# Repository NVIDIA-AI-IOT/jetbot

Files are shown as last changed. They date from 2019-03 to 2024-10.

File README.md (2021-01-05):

# JetBot

<!--[<img src="https://img.shields.io/discord/553852754058280961.svg">](https://discord.gg/Ady6NtF) -->

> Looking for a quick way to get started with JetBot?  Many third party kits are [now available](https://jetbot.org/master/third_party_kits.html)!



JetBot is an open-source robot based on NVIDIA Jetson Nano that is

* **Affordable** - Less than $150 add-on to Jetson Nano
* **Educational** - Tutorials from basic motion to AI based collision avoidance
* **Fun!** - Interactively programmed from your web browser

Building and using JetBot gives the hands on experience needed to create entirely new AI projects.

To get started, read the [JetBot documentation](https://jetbot.org).

## Get involved

We really appreciate any feedback related to JetBot, and also just enjoy seeing what you're working on!  There is a growing community of Jetson Nano and JetBot users.  It's easy to get involved involved...

<!--* Join the [chat server](https://discord.gg/Ady6NtF)-->
* Ask a question and discuss JetBot related topics on the [JetBot GitHub Discussions](https://github.com/NVIDIA-AI-IOT/jetbot/discussions)
* Report a bug by [creating an issue](https://github.com/NVIDIA-AI-IOT/jetbot/issues)
* Share your project or ask a question on the [Jetson Developer Forums](https://devtalk.nvidia.com/default/board/139/jetson-embedded-systems/)

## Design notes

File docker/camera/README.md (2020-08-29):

# Camera Container

This container includes

* A launch script to publish camera images using ZMQ for access in other containers

#### Build

```bash
cd docker/camera
./build.sh
```

#### Run

```bash
cd docker/camera
./enable.sh
```

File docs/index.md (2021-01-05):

# JetBot

<!--[<img src="https://img.shields.io/discord/553852754058280961.svg">](https://discord.gg/Ady6NtF) -->

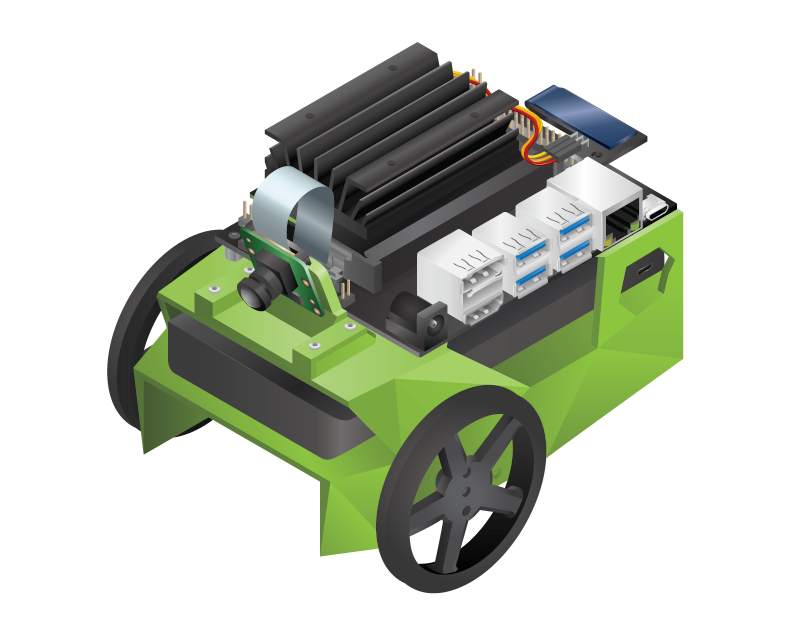
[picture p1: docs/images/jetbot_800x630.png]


<div style="text-align: left;">
    <a href="https://github.com/NVIDIA-AI-IOT/jetbot" class="md-button">Go to GitHub</a>
    <a href="getting_started.html" class="md-button md-button--primary">Get Started</a>
</div>

JetBot is an open-source robot based on NVIDIA Jetson Nano.  You'll like
it because...

## It's Affordable

<div style="display: inline-block">
    
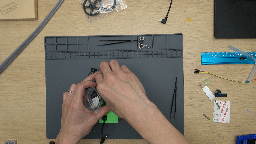
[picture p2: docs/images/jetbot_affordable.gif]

    
JetBot costs less than $250 in parts, <i>including</i> Jetson Nano. The DIY kit includes a bill of materials
which you must purchase and a 3D printed chassis that you can print, or order.  If you're looking to get
up and running as quick as possible, there are also many <a href="third_party_kits.html">third party kits</a> available
that come pre-bundled.

</div>

## It's Educational

<div style="display: inline-block">



JetBot includes a set of <a href="https://jupyter.org/">Jupyter notebooks</a> which cover basic robotics concepts like programatic motor control, to more advanced topics like training a custom AI for avoiding collisions.  What you'll learn isn't limited to JetBot.  You'll learn concepts related to neural network data collection and training that extend as far as your imagination.

</div>

## It's Easy to Setup

<div style="display: inline-block">

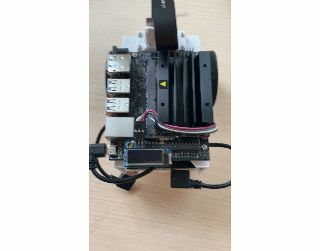
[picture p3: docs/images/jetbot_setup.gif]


JetBot is programmed from your web browser.  Just connect your JetBot to Wifi and launch the JetBot <a href="software_setup/docker.html">Docker container</a>.  This enables JetBot's web programming environment, which is available even after the JetBot reboots.  Once your JetBot boots, just type it's IP address into your web browser and start programming.  

</div>

## It's Fun!

<div style="display: inline-block">



We built JetBot to make exploring ideas related to robotics as fun as possible.  In effect, it's a portable, battery powered
AI computer with a camera that's super easy to program.  This makes it the perfect platform for trying new ideas
related to AI, image processing and robotics.  Our experiments have led us to new projects like <a href="https://github.com/NVIDIA-AI-IOT/jetracer">JetRacer</a>, and we're excited to see where your experiments take you.

</div>

## Get Started

To get started with JetBot, follow the [Getting Started](getting_started.md) instructions.  If you run into any issues along the way, please [let us know](https://github.com/NVIDIA-AI-IOT/jetbot/issues)!

<div style="text-align: right;">
    <a href="https://github.com/NVIDIA-AI-IOT/jetbot" class="md-button">Go to GitHub</a>
    <a href="getting_started.html" class="md-button md-button--primary">Get Started</a>
</div>

## Get involved

We really appreciate any feedback related to JetBot, and also just enjoy seeing what you're working on!  There is a growing community of Jetson Nano and JetBot users.  It's easy to get involved involved...

<!--* Join the [chat server](https://discord.gg/Ady6NtF)-->
* Ask a question and discuss JetBot related topics on the [JetBot GitHub Discussions](https://github.com/NVIDIA-AI-IOT/jetbot/discussions)
* Report a bug by [creating an issue](https://github.com/NVIDIA-AI-IOT/jetbot/issues)
* Share your project or ask a question on the [Jetson Developer Forums](https://devtalk.nvidia.com/default/board/139/jetson-embedded-systems/)

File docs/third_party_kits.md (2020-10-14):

# Third Party Kits

In addition to the open-source DIY version, several third party JetBot kits using Jetson Nano have emerged.  This page details the kits that we're aware of

???+ note 
    Please note, we do not officially maintain these kits in this GitHub project.  Please refer to the vendor's documentation. Please refer to the vendor URL for cost and availability.  Some kits may have additional vendors that we aren't aware of or haven't listed yet.  If you think these would be helpful for other developers to know, please [let us know](../../issues).

## Waveshare JetBot
    
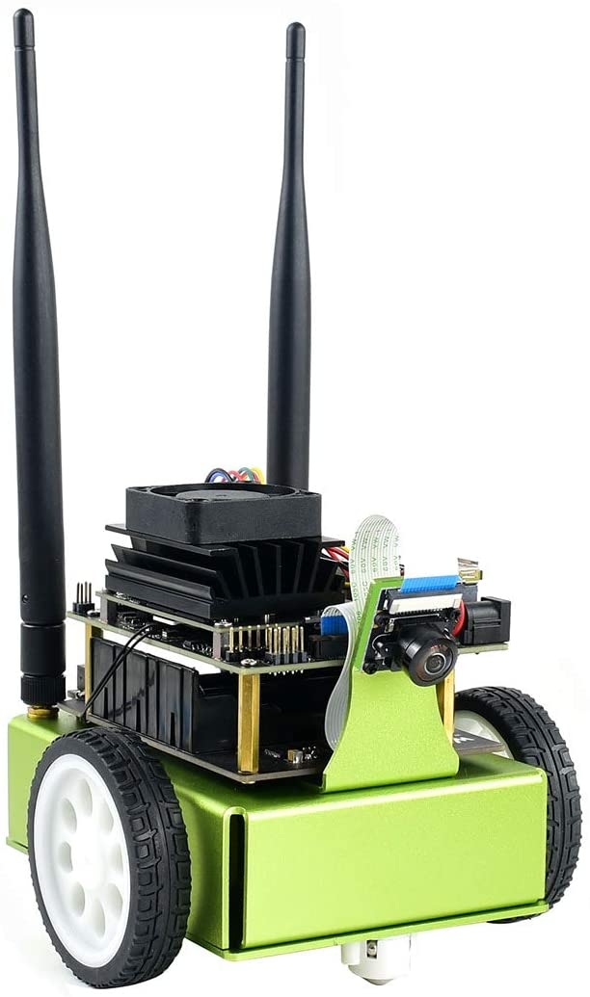
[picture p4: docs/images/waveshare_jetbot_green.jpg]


| Kit | URL |
|---|-----|
| WaveShare JetBot Kit |[Amazon.com](https://www.amazon.com/dp/B081LF98T8/), [Waveshare.com](https://www.waveshare.com/product/mini-pc/jetson/packages/jetbot-ai-kit-acce.htm), [Waveshare.net(中文)](https://www.waveshare.net/shop/JetBot-AI-Kit-Acce.htm) |
| WaveShare JetBot Kit (includes Jetson Nano Dev Kit) | [Amazon.com](https://www.amazon.com/dp/B081LCJXML/), [Waveshare.com](https://www.waveshare.com/product/mini-pc/jetson/packages/jetbot-ai-kit.htm), [Waveshare.net(中文)](https://www.waveshare.net/shop/JetBot-AI-Kit.htm) |

### Links

- [JetBot AI Kit Assemble Manual](https://www.waveshare.com/wiki/JetBot_AI_Kit_Assemble_Manual)
- [JetBot AI Kit](https://www.waveshare.com/wiki/JetBot_AI_Kit)
- [JetBot AI Kit (中文)](https://www.waveshare.net/wiki/JetBot_AI_Kit)

## SparkFun JetBot



| Kit | URL |
|---|-----|
| SparkFun JetBot AI Kit v2.1 | [SparkFun](https://www.sparkfun.com/products/15769) |
| SparkFun JetBot AI Kit v2.1 (includes Jetson Nano Dev Kit) | [SparkFun](https://www.sparkfun.com/products/16417) |

### Links

- [Assembly Guide for SparkFun JetBot AI Kit V2.0](https://learn.sparkfun.com/tutorials/assembly-guide-for-sparkfun-jetbot-ai-kit-v20)

## Seeedstudio JetBot
    


| Kit | URL |
|---|-----|
| Seeedstudio JetBot Smart Car Kit | [Seeedstudio](https://www.seeedstudio.com/Seeedstudio-JetBot-Smart-Car-Kit-p-4055.html) |
| Seeedstudio JetBot Smart Car Kit (includes Jetson Nano Dev Kit) | [Seeedstudio](https://www.seeedstudio.com/Seeedstudio-JetBot-Smart-Car-Powered-by-NVIDIA-Jetson-Nano-p-4054.htm) |

### Links

- [Seeedstudio JetBot Wiring Guide](https://github.com/SeeedDocument/Seeedstudio-Jetbot-Smart-Car/raw/master/res/Seeed%20JetBot%20wiring%20Guide.pdf)
- [Seeedstudio JetBot Setup Guide](https://github.com/SeeedDocument/Seeedstudio-Jetbot-Smart-Car/raw/master/res/Jetbot-snail.docx)

## Silicon Highway JetBot



| Kit | URL |
|---|-----|
| Silicon Highway JetBot Kit | [Silicon Highway (UK)](https://www.siliconhighwaydirect.co.uk/product-p/jetbot-kit.htm) |

## FaBo JetBot
    


| Kit | URL |
|---|-----|
| FaBo JetBot Kit (with Jetson Nano Dev Kit) | [FaBo store (Japan)](https://www.fabo.store/collections/jetbot/products/jetbot-kit) |

### Links

- [JetBot Kit チュートリアル](https://faboplatform.github.io/JetbotDocs/)

## GPUS JetBot
    


| Kit | URL |
|---|-----|
| GPUS JetBot Kit (with Jetson Nano Dev Kit) | [Taobao](https://item.taobao.com/item.htm?id=602196310625) |

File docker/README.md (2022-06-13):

# JetBot Docker

This directory contains scripts to build the JetBot docker containers.  

## Quick Start

### Step 1 - Configure System

First, call the ``scripts/configure_jetson.sh`` script to configure the power mode and other parameters.

```bash
cd jetbot
./scripts/configure_jetson.sh
```

Next, source the ``docker/configure.sh`` script to configure various environment variables related to JetBot docker.

```bash
cd docker
source configure.sh
```

Depending on your Jetson L4T version, you may get a similar warning :

```bash
JETBOT_BASE_IMAGE not found for 32.6.1.  Please manually set the JETBOT_BASE_IMAGE environment variable. (ie: export JETBOT_BASE_IMAGE=...)
```

In the case of ``32.6.1``, the following container will work :

```bash
export JETBOT_BASE_IMAGE=nvcr.io/nvidia/l4t-pytorch:r32.6.1-pth1.9-py3
```

Refer to ``https://ngc.nvidia.com/catalog/containers/nvidia:l4t-pytorch`` for more details.

Finally, if you haven't already, set the default docker runtime to NVIDIA.  This is needed to use
CUDA related components with the containers.

```bash
./set_nvidia_runtime.sh
```

If needed, you can also set memory limits on the Jupyter container.

```bash
export JETBOT_JUPYTER_MEMORY=500m
export JETBOT_JUPYTER_MEMORY_SWAP=3G
```

### Step 2 - Building Containers

If you want to build the containers from scratch, simply call :

```bash
./build.sh
```

### Step 3 - Enable All Containers

Call the following to enable the JetBot docker containers 

```bash
sudo systemctl enable docker   # enable docker daemon at boot
./enable.sh $HOME   # we'll use home directory as working directory, set this as you please.
```

Now you can go to ``https://<jetbot_ip>:8888`` from a web browser and start programming JetBot!
You can do this from any machine on your local network.  The password to log in is ``jetbot``.



> Note: The directory you specify to ``./enable.sh`` will be mounted as a volume in the jupyter container 
at the location ``/workspace``.  This means the work you in the ``/workspace`` folder inside container
is saved.  This is set to the root directory of Jupyter Lab.  Please note, if you work outside of that directory it will be lost when the container shuts down.

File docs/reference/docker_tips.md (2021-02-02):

# Docker Tips

This page provides various information related to using docker with JetBot.

## Establishing access to the Docker host terminal

The Jupyter Lab is running in the Docker container, thus the **Terminal** you open on Jupyter Lab only have access to the container environment.<br>
This means you cannot use commands like `nvpmodel`, `tegrastats`, `journalctl`, `systemctl` and others.

To get around this limitation, you can actually SSH in to the Docker host machine by;

```
ssh jetbot@0.0.0.0
```

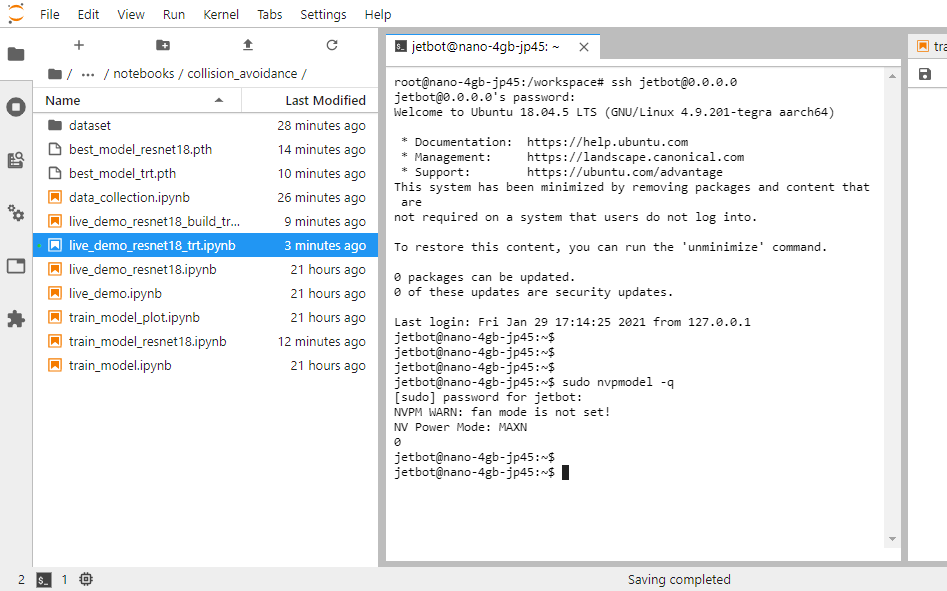
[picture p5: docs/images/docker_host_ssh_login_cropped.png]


## Using Nvidia GPU Cloud (NGC)

The standard JetBot containers are hosted on docker hub, but for development or testing purposes, you may wish to use Nvidia GPU Cloud. To access containers on NGC, you need to sign into the NGC registry. To do this:

1. Log into ngc.nvidia.com

2. Generated your API Key

    1. Navigate to Setup > API Key
    2. Click on "Generate API Key" at the right upper corner of the page
    3. Copy the API key for future use

3. On your Jetson, sign into the NGC registry using the generated key

    ```bash
    $ sudo docker login nvcr.io
    
    Username: $oauthtoken
    Password: <Your Generated Key>
    ```

For the username, enter `$oauthtoken` exactly as shown. It is a special authentication token for all users.

## Using custom Jupyter Lab workspace directory

The argument you provide to the enable.sh script is mounted as a volume inside the docker container. Inside the docker container, this volume is located at /workspace. Any changes that you make inside this directory will be saved outside of the docker container. To use a different directory as the workspace for the Jupyter contianer, just provide the path as an argument when calling enable.sh. For example, to set the workspace to your home directory, you would do

```bash
cd jetbot/docker
./enable.sh $HOME
```

## Disabling containers

Once you execute the `enable.sh` script, the containers are set to restart automatically.
This means you can shut down your Jetson, and when you reboot the containers will run and you don't need to repeat this process. 

To prevent the containers from starting automatically, just call the disable.sh script.

```bash
cd ~/jetbot/docker
./disable.sh
```

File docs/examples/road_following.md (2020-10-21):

# Road Following

In this example we'll collect an *image regression* dataset that will enable JetBot to follow a road!  We'll teach JetBot to detect a target ``x, y`` image coordinate that the JetBot will chase.  As JetBot gets closer to the point, it moves further along the track.

#### Step 1 - Collect data on JetBot

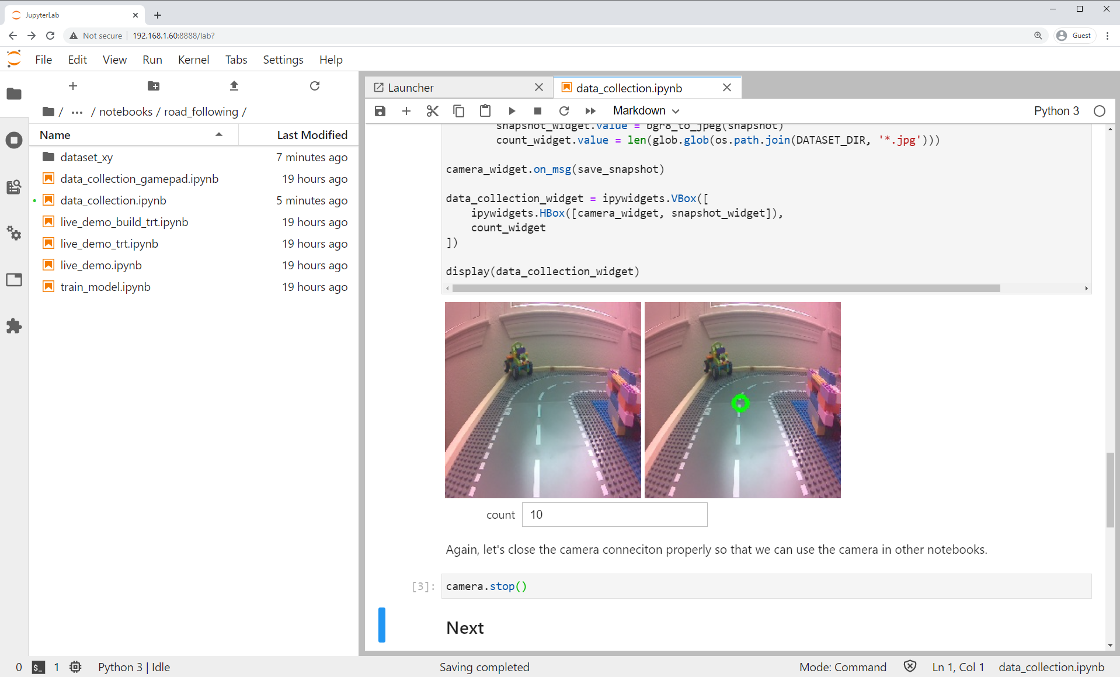
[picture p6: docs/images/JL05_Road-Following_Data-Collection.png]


1. Connect to your robot by navigating to ``http://<jetbot_ip_address>:8888``
2. Sign in with the default password ``jetbot``
2. Shutdown all other running notebooks by selecting ``Kernel`` -> ``Shutdown All Kernels...``
3. Navigate to ``~/Notebooks/road_following/``
4. Open and follow the ``data_collection.ipynb`` notebook

#### Step 2 - Train neural network

##### Option 1 - Train on Jetson Nano
1. Connect to your robot by navigating to ``http://<jetbot_ip_address>:8888``
2. Sign in with the default password ``jetbot``
3. In the Jupyter Lab tab, navigate to ``~/Notebooks/road_following``
4. Open and follow the [``train_model.ipynb``](https://github.com/NVIDIA-AI-IOT/jetbot/blob/master/notebooks/road_following/train_model.ipynb) notebook

##### Option 2 - Train on other GPU machine
1. Connect to a GPU machine with PyTorch installed and a Jupyter Lab server running

2. Upload the road following avoidance [training notebook](https://github.com/NVIDIA-AI-IOT/jetbot/blob/master/notebooks/road_following/train_model.ipynb) to this machine
3. Open and follow the ``train_model.ipynb`` notebook

#### Step 3 - Optimize the model on Jetson Nano

1. Connect to your robot by navigating to ``https://<jetbot_ip_address>:8888``
2. Sign in with the default password ``jetbot``
3. Shutdown all other running notebooks by selecting ``Kernel`` -> ``Shutdown All Kernels...``
4. Navigate to ``~/Notebooks/road_following``
5. Open and follow the ``live_demo_build_trt.ipynb`` notebook to optimize the model with TensorRT

#### Step 4 - Run live demo on JetBot

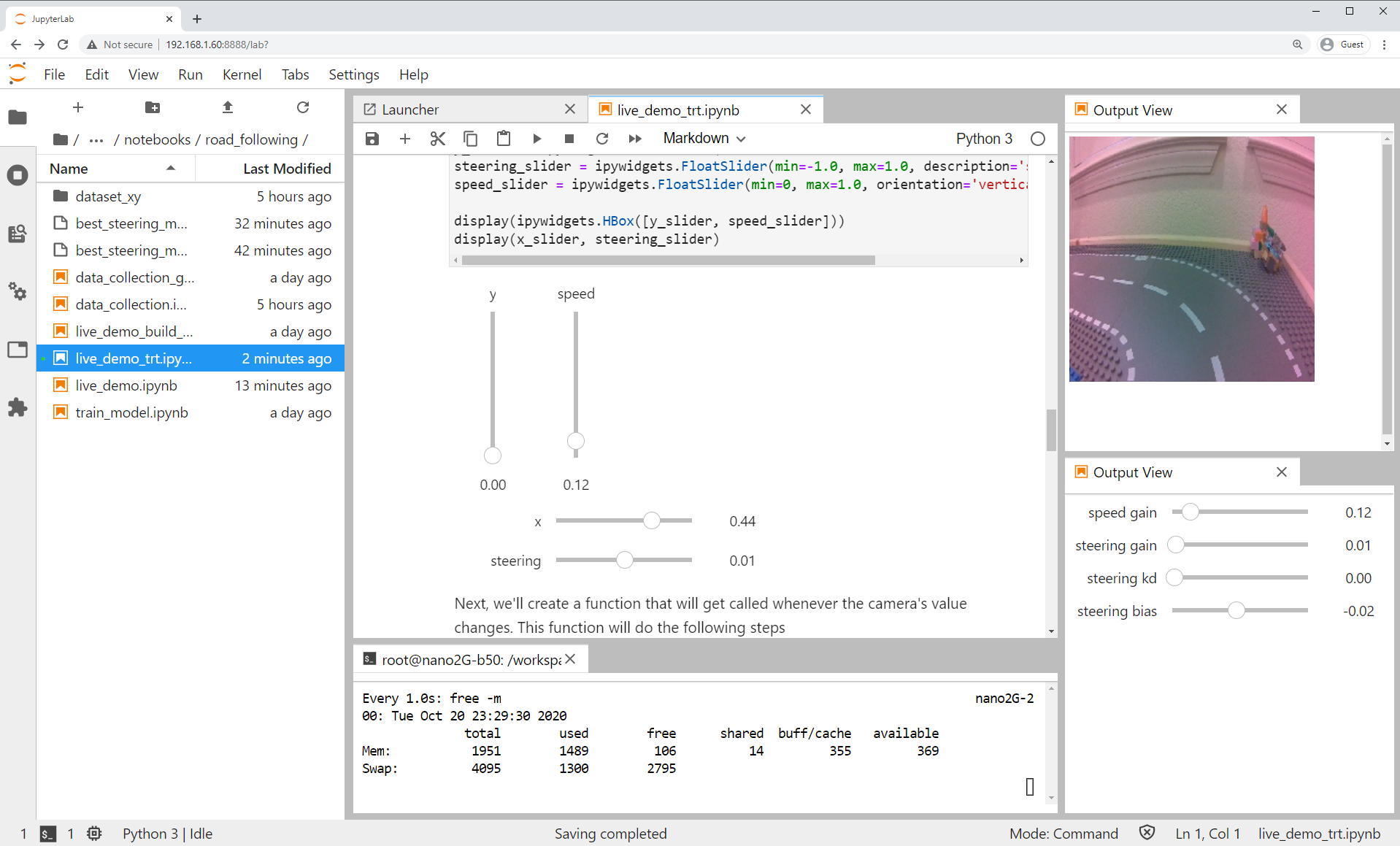
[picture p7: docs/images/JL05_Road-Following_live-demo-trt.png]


1. Connect to your robot by navigating to ``http://<jetbot_ip_address>:8888``
2. Sign in with the default password ``jetbot``
3. Shutdown all other running notebooks by selecting ``Kernel`` -> ``Shutdown All Kernels...``
4. Navigate to ``~/Notebooks/road_following``
5. Open and follow the ``live_demo_trt.ipynb`` notebook to run the optimized model

???+ warning
    Start cautious and give JetBot enough space to move around.

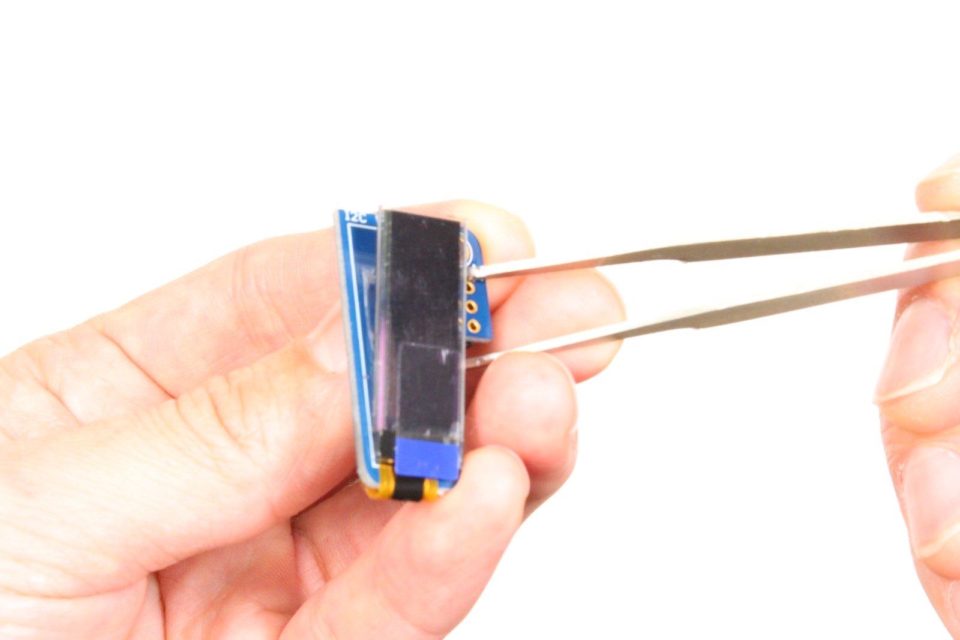
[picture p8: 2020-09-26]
docs/images/JB3-Assy_10-1.JPG

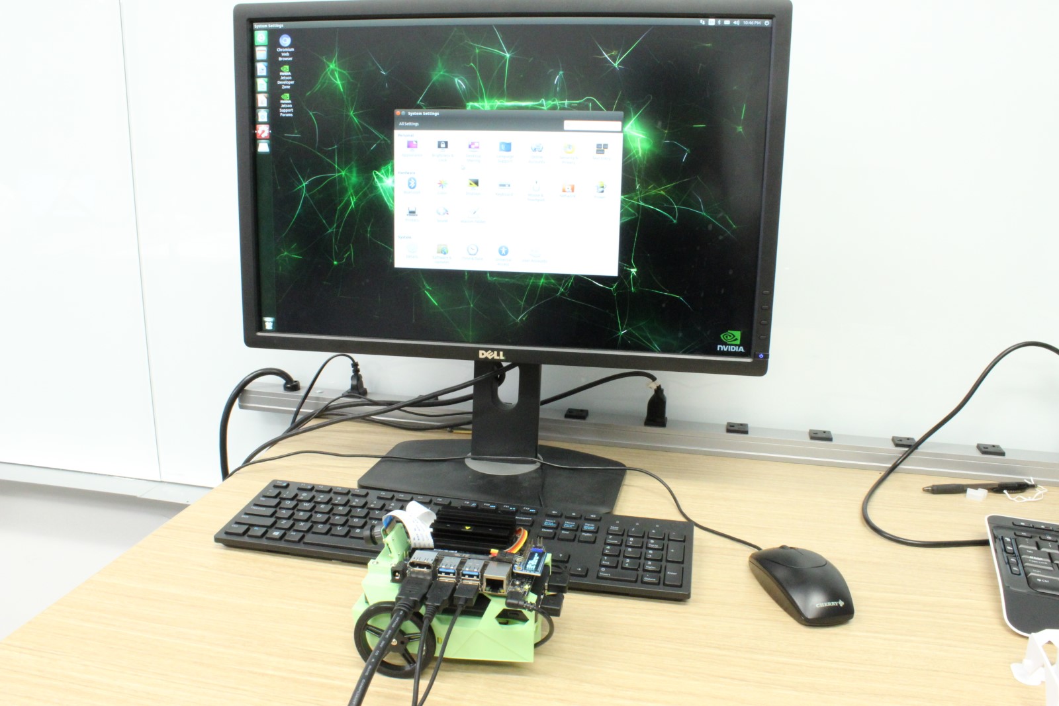
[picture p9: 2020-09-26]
docs/images/JB3-Assy_16-3.JPG

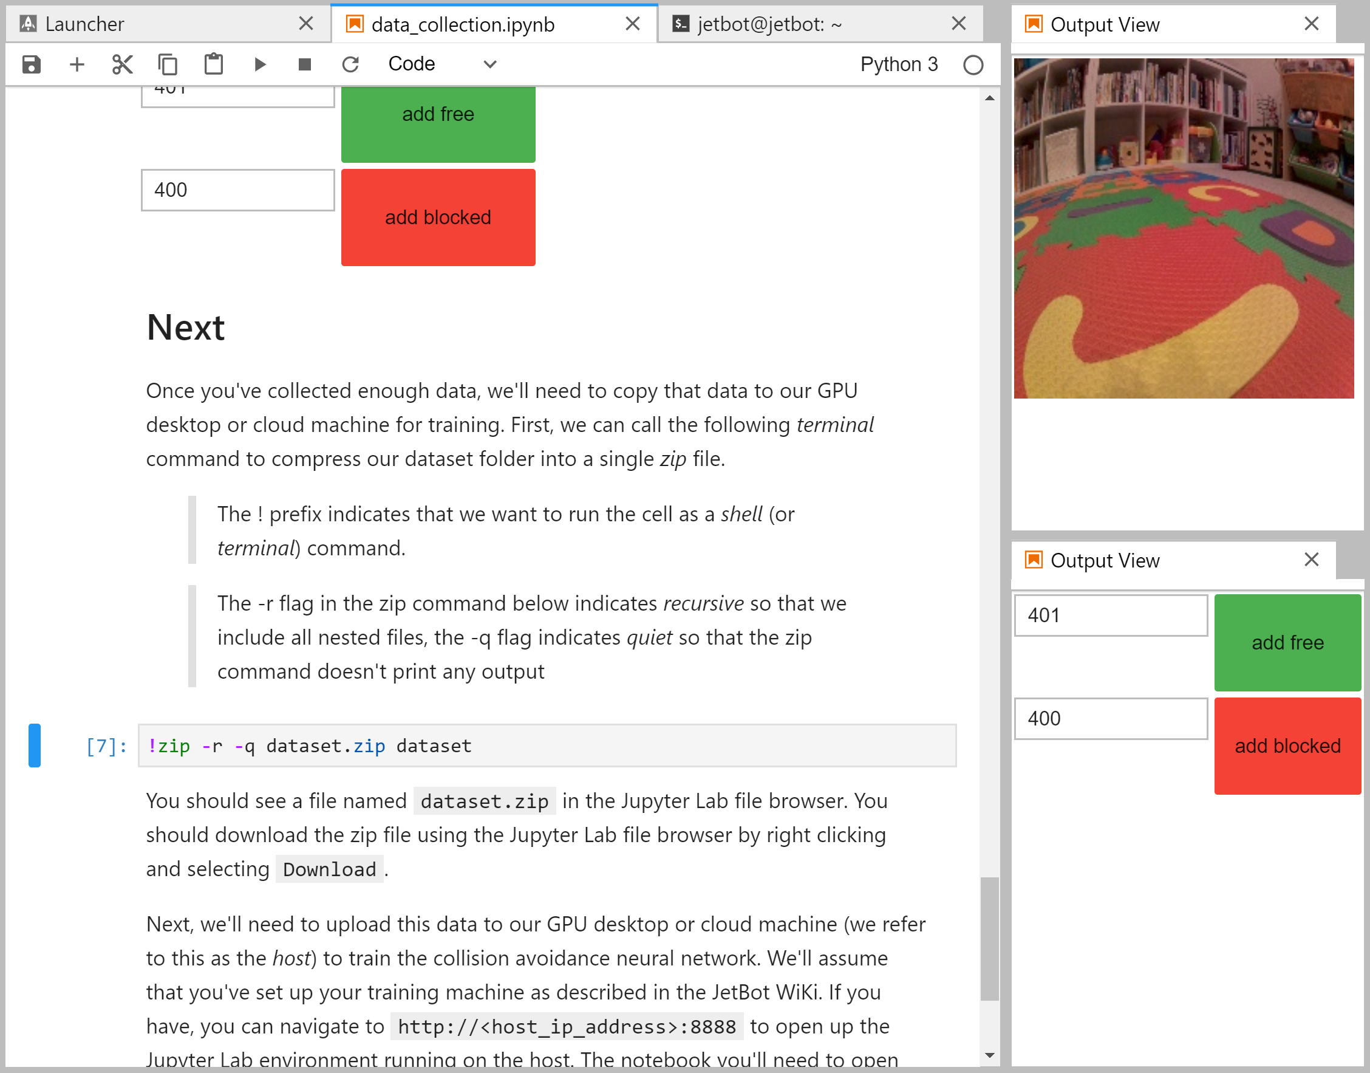
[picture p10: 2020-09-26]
docs/images/JL03a_Data-Collection_thumb.png

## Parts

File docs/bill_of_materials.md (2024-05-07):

!!! note

    JetBot was originally designed with ***Jetson Nano Developer Kit***, which was [discontinued](https://forums.developer.nvidia.com/t/jetson-nano-developer-kit-eol/276729).

    For those newly starting, we recommend planning the JetBot assembly with **Jetson Orin Nano 8GB Developer Kit**.<br>
    The Bill of Materials for Orin version of JetBot is laid out on [Bill of Materials (Orin)](./bill_of_materials_orin.md) page.

    Please note that, currently, the software for the Orin version of JetBot is still work in progress.

This page lists everything you need to build JetBot, along with purchasing links from popular vendors.

Some of the parts are 3D printed.  We provide the STL files needed to print these parts.  Please see our [3d printing](3d_printing.md) page for tips on printing.

### Common parts

You need these components for each JetBot.

|  **Part** | **Quantity** | **Cost** | **URL** | **Notes** |
| --- | --: | --: | --- | --- |
| Jetson Nano | 1 |  $99.00 | [NVIDIA](https://developer.nvidia.com/embedded/buy/jetson-nano-devkit)  |  |
| Micro SD card | 1 | $13.99 | [Amazon](https://amzn.to/2Us6bOv) | 64GB |
| Power supply | 1 | $7.50 | [Adafruit](http://bit.ly/af1995) | Micro USB, 5V, 2.5A |
| Motor | 2 | $5.90 | [Adafruit](http://adafru.it/3777), [Amazon(1)](https://amzn.to/2MYln32), [Amazon(2)](https://amzn.to/2MU9zPb) | "TT" form factor |
| Motor Driver | 1 | $19.95 | [Adafruit](http://adafru.it/2927), [Amazon](https://amzn.to/2GvJhBA) |  |
| Caster ball | 1 | $6.30 | [Amazon](http://amzn.com/B01N2S7CX6/) | 1-inch diameter |
| Battery | 1 | $15.99 | [Amazon](https://amzn.to/2WRcIUe) | 2x 5V/3A output, 10,000mAh |
| USB cable pack | 1 | $6.99 | [Amazon](http://amzn.com/B01N337FQF/) | Type A to Micro, right angle |
| *PiOLED* display | 1 | $14.95 | [Adafruit](http://adafru.it/3527), [Amazon](https://amzn.to/2GgxUxX) |  |
| *PiOLED* header | 1 | $5.95 | [Adafruit](http://adafru.it/1541), [Amazon](https://amzn.to/2taLSJf), [Sparkfun](https://www.sparkfun.com/products/12792) | 2x(3+) right angle male |
| Chassis | 1 | -- | [STL file](cad/chassis.stl) | see [3D printing](3d-printing) | |
| Camera Mount | 1 | -- | [STL file](cad/camera_mount.stl) | see [3D printing](3d-printing) |

### Camera

You need a camera with appropriate sensor and field of view for each JetBot.  Select an option and get the parts specified.

#### Option 1 (default) - Leopard Imaging Camera

|  **Part** | **Quantity** | **Cost** | **URL** | **Notes** |
| --- | --: | --: | --- | --- |
| Camera | 1 | $29.00 | [Leopard Imaging](https://leopardimaging.com/product/li-imx219-mipi-ff-nano/) | LI-IMX219-MIPI-FF-NANO-**H145**|

#### Option 2 - IMX219-160 Camera

|  **Part** | **Quantity** | **Cost** | **URL** | **Notes** |
| --- | --: | --: | --- | --- |
| Camera | 1 | $29.90 | [Amazon](http://amzn.com/B07T43K7LC/) | IMX219-160 Camera |

#### Option 3 - RPi Camera V2 + Lens Attachment

|  **Part** | **Quantity** | **Cost** | **URL** | **Notes** |
| --- | --: | --: | --- | --- |
| Camera | 1 | $23.90 | [Amazon](https://amzn.to/2MSi6lL), [Adafruit](http://adafru.it/3099) | Raspberry Pi Camera V2 |
| Camera lens attachment | 1 | $18.99 | [Amazon(1)](https://amzn.com/B07HMXJ9Y1), [Amazon(2)](https://amzn.com/B07HF81BVL/), [eBay](https://ebay.us/Fz7HGd) | 160-degree FoV |

### WiFi

You need a WiFi solution for each JetBot.  Select an option and get the parts specified.

#### Option 1 (default) - M2 Card + Antennas

This option is a good choice if you're building JetBot with the original Jetson Nano 4GB.  It has been widely tested and used for JetBot.

???+ attention

    Jetson Nano 2GB does not have a M.2 connector, so this option will not work with it.

|  **Part** | **Quantity** | **Cost** | **URL** | **Notes** |
| --- | --: | --: | --- | --- |
| WiFi card | 1 | $18.95 | [Amazon](https://amzn.to/2WKEkum), [NewEgg](https://www.neweggbusiness.com/Product/Product.aspx?Item=9SIV21M85N2699) | M2, Intel Wireless-AC 8265 |
| WiFi antenna | 2 | $5.06 | [Arrow](https://www.arrow.com/en/products/2042811100/molex) | U.FL connectors |

#### Option 2 - USB Dongle

This option is compatible with both the original Jetson Nano (4GB) and Jetson Nano 2GB.

|  **Part** | **Quantity** | **Cost** | **URL** | **Notes** |
| --- | --: | --: | --- | --- |
| WiFi Dongle - TP-Link Archer T2U Nano | 1 | $17.99 | [Amazon](https://amzn.com/B07PB1X4CN/) | RTL8811AU chipset |
| WiFi Dongle - TP-Link Archer T2U Plus | 1 | $19.99 | [Amazon](https://amzn.com/B07P5PRK7J/) | RTL8811AU chipset |

???+ info
    For other possible USB Wi-fi dongles that you can use on Jetson Nano, please check the Suported Components List.

    - [Jetson Nano 2GB Developer Kit User Guide - Supported Component List](https://developer.nvidia.com/embedded/learn/jetson-nano-2gb-devkit-user-guide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)

### Wheels

You need wheels with a "TT" motor shaft connector for each JetBot.  Select an option and get the parts specified.

#### Option 1 - 60mm

|  **Part** | **Quantity** | **Cost** | **URL** | **Notes** |
| --- | --: | --: | --- | --- |
| Wheel | 2 | $5.00 | [Adafruit](http://adafru.it/3757) | 60mm diameter |
| Caster base | 1 | -- | [STL file](cad/caster_base_60mm.stl) | for 60mm wheel |
| Caster shroud | 1 | -- | [STL file](cad/caster_shroud_60mm.stl) | for 60mm wheel |

#### Option 2 - 65mm

|  **Part** | **Quantity** | **Cost** | **URL** | **Notes** |
| --- | --: | --: | --- | --- |
| Wheel | 2 | $3.00 | [Adafruit](https://www.adafruit.com/product/3763) | 65mm diameter |
| Caster base | 1 | -- | [STL file](cad/caster_base_65mm.stl) | for 65mm wheel|
| Caster shroud | 1 | -- | [STL file](cad/caster_shroud_65mm.stl) | for 65mm wheel |

### Assembly Hardware

You need the following parts to build JetBot.  They come in packs, so order the quantity you need for the number of JetBots you are going to build.

|  **Part** | **Qty per JetBot** | **Qty per pack** | **Cost per JetBot** | **URL** | **Notes** |
| --- | --- | --: | --: | --: | --- |
|  Adhesive pads | 2 | 48 | $0.14 | [Amazon](http://amzn.com/B01FIK56Q4) | |
|  M2 screw | 20 | 100 | $1.29 | [Amazon](http://amzn.com/B00YBMRAH4) | 8mm long, self tapping |
|  M3 screw | 4 | 60 | $0.47 | [Amazon](https://amzn.to/2tcdluk) | 25mm long|
|  M3 nut | 4 | 100 | $0.24 | [Amazon](https://amzn.to/2tb8PMo) |  |
|  Jumper wires | 4 | 40 | $0.13 | [Amazon](https://amzn.to/2tacYQD) | Female-female, ~20cm |

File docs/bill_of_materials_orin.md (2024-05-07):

# Bill of Materials - Jetson Orin Nano version

!!! note

    JetBot was originally designed with ***Jetson Nano Developer Kit***, which was [discontinued](https://forums.developer.nvidia.com/t/jetson-nano-developer-kit-eol/276729).

    For those newly starting, we recommend planning the JetBot assembly with **Jetson Orin Nano 8GB Developer Kit**. 

    Please note that, currently, the software for the Orin version of JetBot is still work in progress.

This page lists all the parts you need to build the open-source JetBot with the new [**Jetson Orin Nano 8GB Developer Kit**](https://developer.nvidia.com/embedded/learn/get-started-jetson-orin-nano-devkit), along with purchasing links from popular vendors.

Some of the parts are 3D printed.  We provide the STL files needed to print these parts.  Please see our [3d printing](3d_printing.md) page for tips on printing.

### Common parts

You need these components for each JetBot.

|  **Part** | **Quantity** | **Cost** | **URL** | **Notes** |
| --- | --: | --: | --- | --- |
| Jetson Orin Nano 8GB Developer Kit | 1 |  $499.00 | [NVIDIA](https://store.nvidia.com/jetson/store/)  |  |
| Micro SD card | 1 | $14.95 | [Amazon](https://a.co/d/0aOqPQh) | 128GB |
| Motor | 2 | $5.90 | [Adafruit](http://adafru.it/3777), [Amazon(1)](https://a.co/d/cQ489BJ), [Amazon(2)](https://amzn.to/2MU9zPb) | "TT" form factor |
| Motor Driver | 1 | $19.95 | [Adafruit](http://adafru.it/2927), [Amazon](https://a.co/d/aUs8dwA) |  |
| Caster ball | 1 | $10.99 | [Amazon](https://a.co/d/3WmVtqU) | 1-inch diameter |
| USB cable pack | 1 | $6.99 | [Amazon](http://amzn.com/B01N337FQF/) | Type A to Micro, right angle |
| *PiOLED* display | 1 | $13.45 | [Adafruit](http://adafru.it/3527), [Amazon](https://a.co/d/cmRS0RE) |  |
| *PiOLED* header | 1 | $7.99 | [Adafruit](http://adafru.it/1541), [Amazon](https://a.co/d/fGDbnIE), [Sparkfun](https://www.sparkfun.com/products/12792) | 2x(3+) right angle male |
| Chassis | 1 | -- | [STL file](cad/chassis.stl) | see [3D printing](3d-printing) | |
| Camera Mount | 1 | -- | [STL file](cad/camera_mount.stl) | see [3D printing](3d-printing) |

### Power source

|  **Part** | **Quantity** | **Cost** | **URL** | **Notes** |
| --- | --: | --: | --- | --- |
| Battery | 1 | $12.99 | [Amazon](https://a.co/d/5DvsXGu) | PD 20W output, 10,000mAh |
| USB-C PD cable | 1 | $10.99 | [Amazon](https://a.co/d/ihjA431) | USB-C to DC 5.5mm x 2.5mm, right angle |

!!! note

    With this power source option, we recommend setting Jetson Orin Nano in `7W` mode (`sudo nvpmodel -m 1`), as we observed Jetson in `15W` mode shutdown in certain scenarios like suddenly ramping up the motor from 0% to 100% speed or having motors stalled.

### Camera

You need a camera module with 22pin cable for interfacing to Jetson Orin Nano 8GB Developer Kit carrier board and the appropriate wide field of view for each JetBot.  

Select an option and get the parts specified.

#### Option 1 (default) - IMX219 175-degree FoV camera

|  **Part** | **Quantity** | **Cost** | **URL** | **Notes** |
| --- | --: | --: | --- | --- |
| Camera | 1 | $19.99 | [ArduCam](https://www.arducam.com/product/8mp-imx219-175-degree-ultra-wide-angle-raspberry-pi-b0392/), [Amazon](https://a.co/d/gbWtB9X) | ArduCam B0392 - IMX219 175-degree |

<!-- #### Option 2 - IMX477 12.3MP 88°(D)×75°(H)

|  **Part** | **Quantity** | **Cost** | **URL** | **Notes** |
| --- | --: | --: | --- | --- |
| Camera | 1 | $64.99 | [ArduCam](https://www.arducam.com/product/arducam-high-quality-camera-for-jetson-nano-and-xavier-nx-12mp-m12-mount/), [Amazon](https://a.co/d/gIJkaBO) | ArduCam B0251 - IMX477 12.3MP 88°(D)×75°(H) | -->

### Wheels

You need wheels with a "TT" motor shaft connector for each JetBot.  Select an option and get the parts specified.

#### Option 1 - 60mm

|  **Part** | **Quantity** | **Cost** | **URL** | **Notes** |
| --- | --: | --: | --- | --- |
| Wheel | 2 | $5.00 | [Adafruit](http://adafru.it/3757) | 60mm diameter |
| Caster base | 1 | -- | [STL file](cad/caster_base_60mm.stl) | for 60mm wheel |
| Caster shroud | 1 | -- | [STL file](cad/caster_shroud_60mm.stl) | for 60mm wheel |

#### Option 2 - 65mm

|  **Part** | **Quantity** | **Cost** | **URL** | **Notes** |
| --- | --: | --: | --- | --- |
| Wheel | 2 | $3.00 | [Adafruit](https://www.adafruit.com/product/3763) | 65mm diameter |
| Caster base | 1 | -- | [STL file](cad/caster_base_65mm.stl) | for 65mm wheel|
| Caster shroud | 1 | -- | [STL file](cad/caster_shroud_65mm.stl) | for 65mm wheel |

### Assembly Hardware

You need the following parts to build JetBot.  They come in packs, so order the quantity you need for the number of JetBots you are going to build.

|  **Part** | **Qty per JetBot** | **Qty per pack** | **Cost per JetBot** | **URL** | **Notes** |
| --- | --- | --: | --: | --: | --- |
| Adhesive Strips (Poster Strips) | 2 | 60 | $0.14 | [Amazon](https://a.co/d/0vJTr7M) | |
|  M2 screw | 20 | 100 | $1.40 | [Amazon](https://a.co/d/cyiag7K) | 8mm long, self tapping |
|  M3 screw | 4 | 60 | $0.47 | [Amazon](https://a.co/d/2foBYX5) | 25mm long|
|  M3 nut | 4 | 150 | $0.20 | [Amazon](https://a.co/d/05wzwMC) |  |
|  Jumper wires | 4 | 40 | $0.56 | [Amazon](https://a.co/d/5FdEzo4) | Female-female, ~20cm |

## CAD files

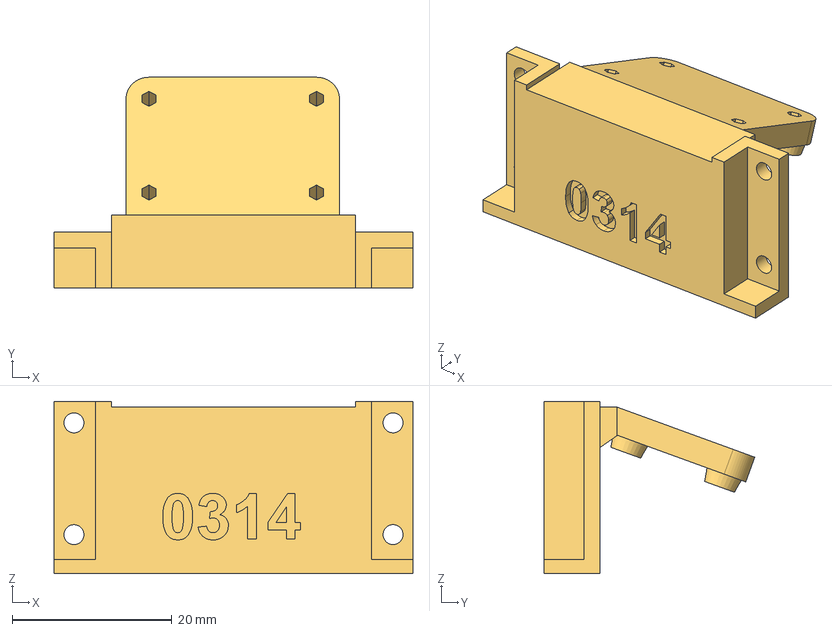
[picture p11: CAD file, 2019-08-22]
assets/camera_mount.step
45.0 x 26.4 x 21.6 mm

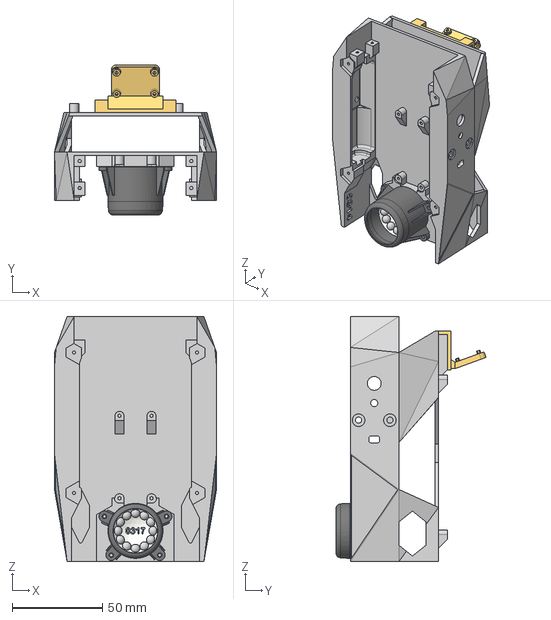
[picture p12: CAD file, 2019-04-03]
assets/jetbot_60mm.step
90.0 x 83.4 x 136.0 mm

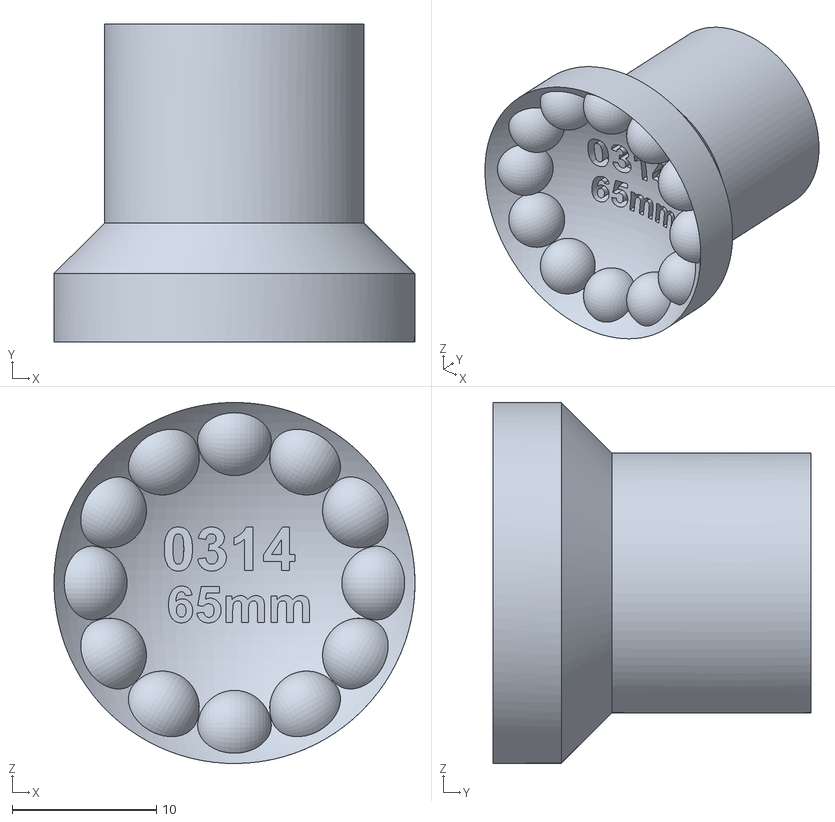
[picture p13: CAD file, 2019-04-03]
assets/caster_base_65mm.stl
25.0 x 22.0 x 25.0

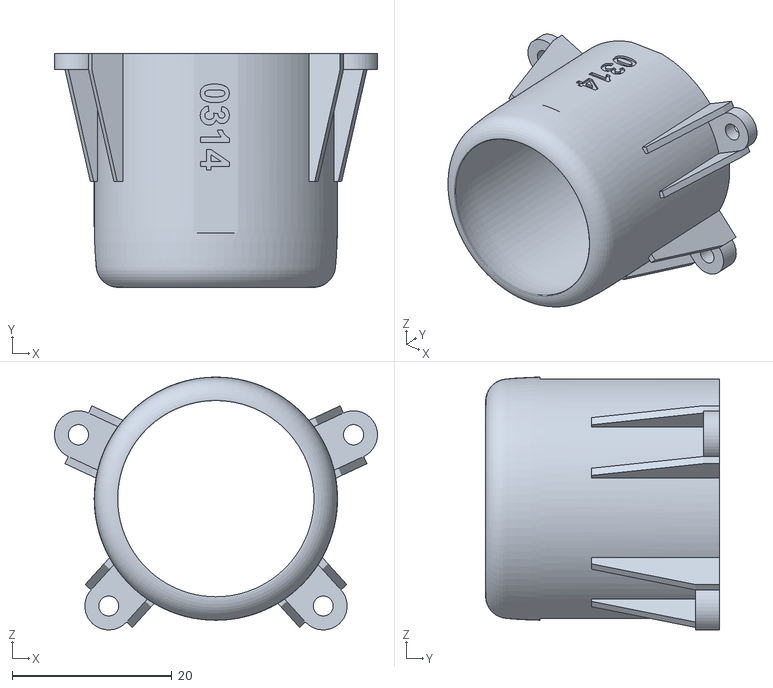
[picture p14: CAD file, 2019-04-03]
assets/caster_shroud_65mm.stl
40.5 x 29.3 x 31.7

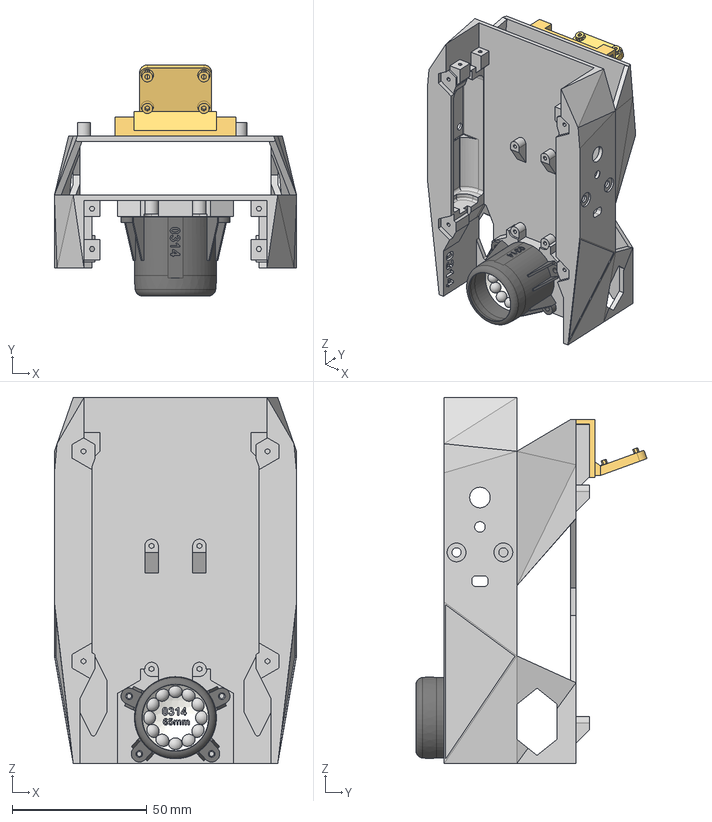
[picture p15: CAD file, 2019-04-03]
assets/jetbot_65mm.step
90.0 x 85.9 x 136.0 mm

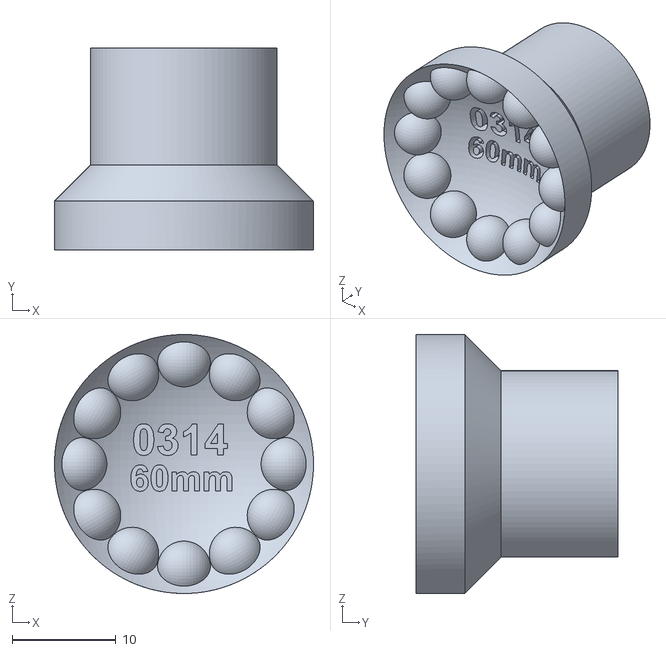
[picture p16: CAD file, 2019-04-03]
assets/caster_base_60mm.stl
25.0 x 19.5 x 25.0

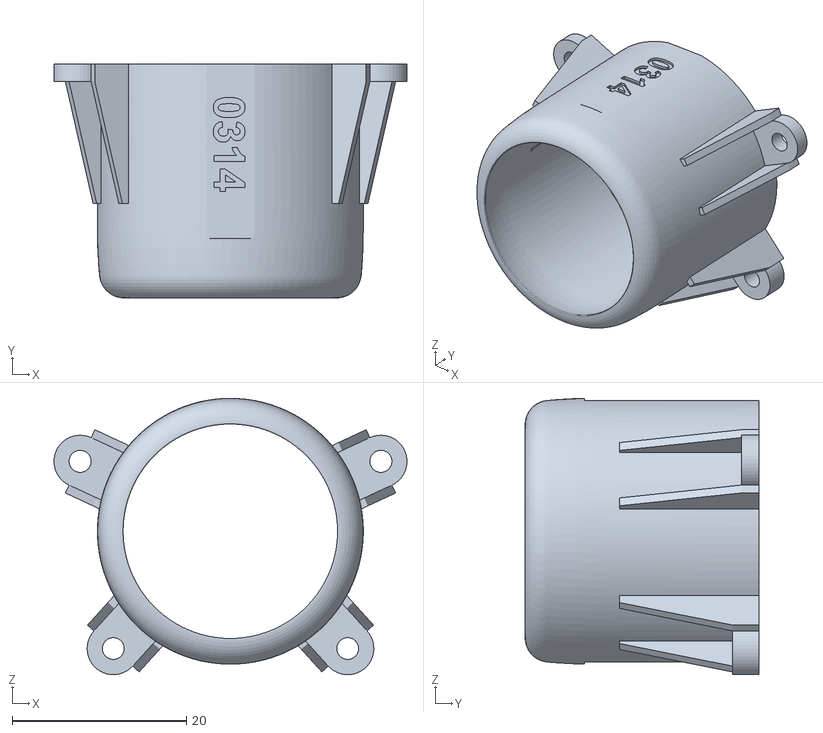
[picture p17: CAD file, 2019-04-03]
assets/caster_shroud_60mm.stl
40.5 x 26.8 x 31.7

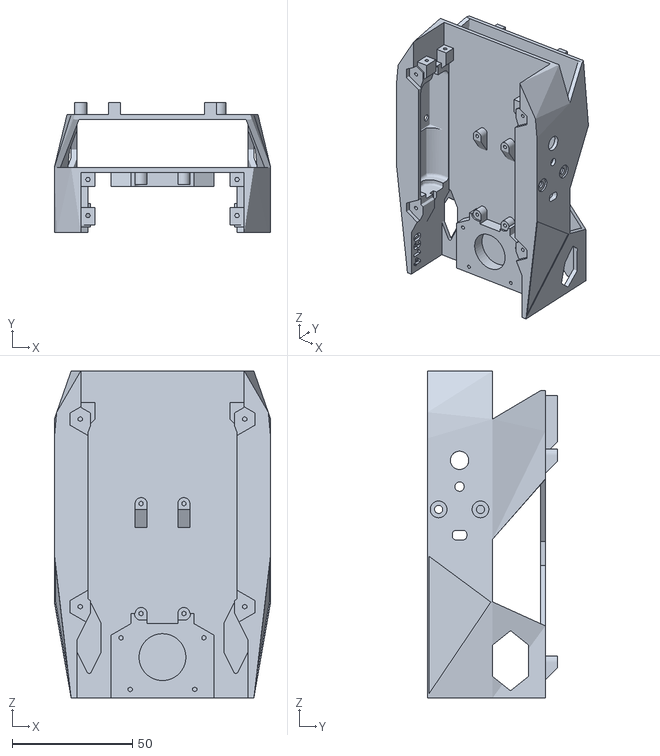
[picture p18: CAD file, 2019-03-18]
assets/chassis.stl
90.0 x 54.0 x 136.0

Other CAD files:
assets/camera_mount.iges
assets/camera_mount.stl

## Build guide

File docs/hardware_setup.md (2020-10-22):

This page details the hardware setup instructions for creating JetBot

## Tools needed

To build JetBot you'll need the following tools

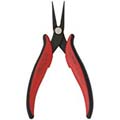
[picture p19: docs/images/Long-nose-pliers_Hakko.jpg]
Long-nose-pliers_Hakko
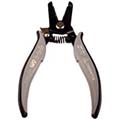
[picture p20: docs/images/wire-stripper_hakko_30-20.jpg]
wire-stripper_hakko_30-20
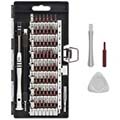
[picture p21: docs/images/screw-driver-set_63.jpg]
screw-driver-set_63
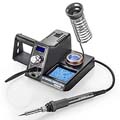
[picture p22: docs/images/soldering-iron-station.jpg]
soldering-iron-station
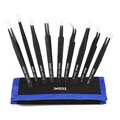
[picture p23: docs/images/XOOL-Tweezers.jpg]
XOOL-Tweezers


* Pliers

* Wire flush cutters/wire stripper
* Phillips screwdriver (+ [Hex screwdriver for M2 hex socket screws](https://amzn.com/B00CP2GGBI/) )
* Soldering iron and solder
* (optional) [Precision Electronics Tweezers](https://amzn.to/2t4AWg7)

## Assembly

### Step 1 - Clean 3D printed parts

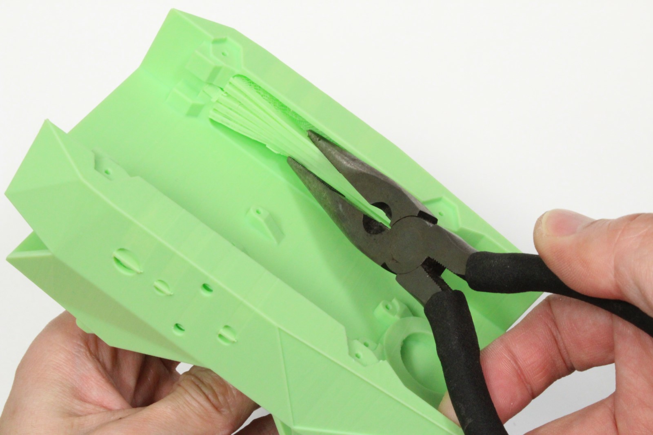
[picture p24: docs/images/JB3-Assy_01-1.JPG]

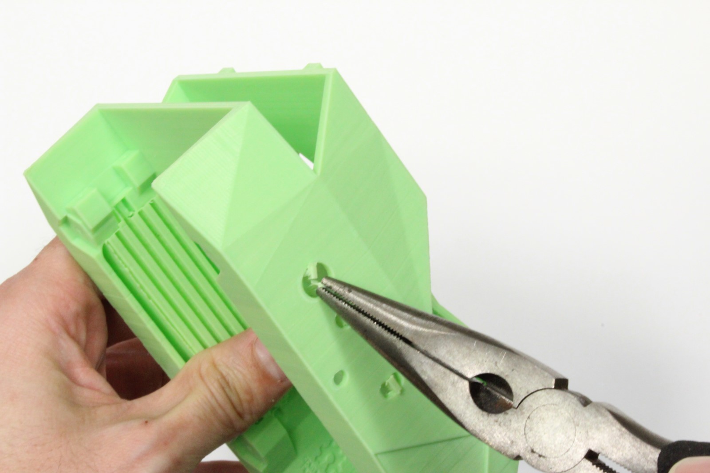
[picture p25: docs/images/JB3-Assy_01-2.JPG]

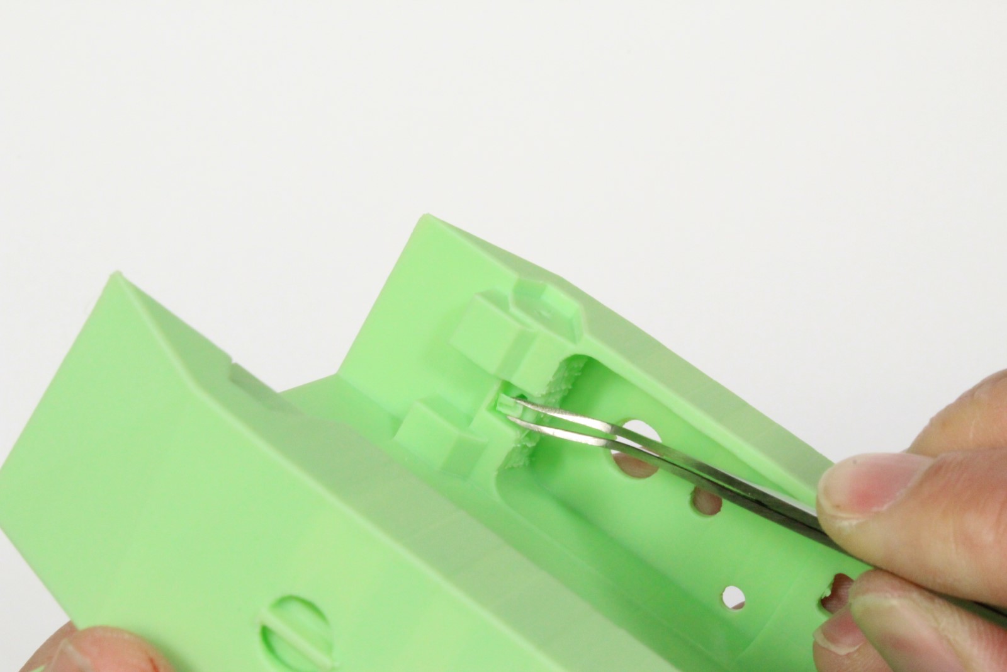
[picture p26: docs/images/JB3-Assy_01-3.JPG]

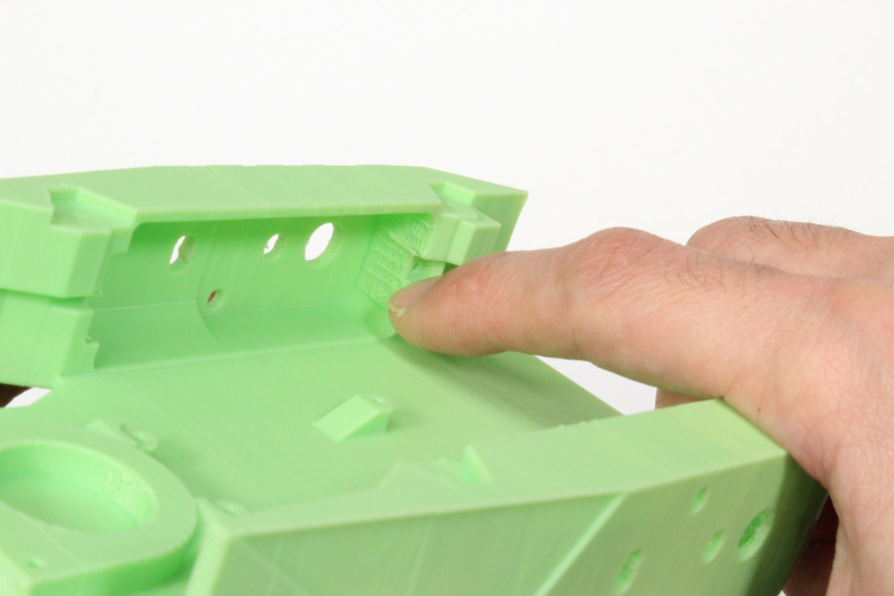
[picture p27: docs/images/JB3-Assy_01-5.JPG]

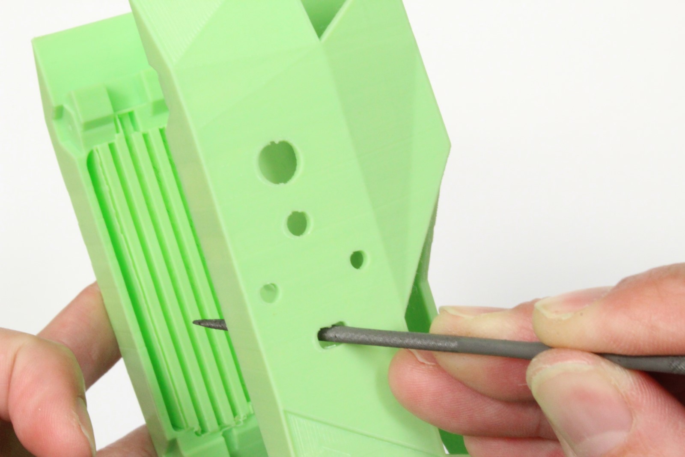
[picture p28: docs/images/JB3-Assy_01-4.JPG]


1. Remove support material from motor sockets using pliers

2. Remove support material from all surfaces, openings and screw holes using pliers, tweezers, and/or fingernails
3. File material from openings if they are too tight

### Step 2 - Mount motors

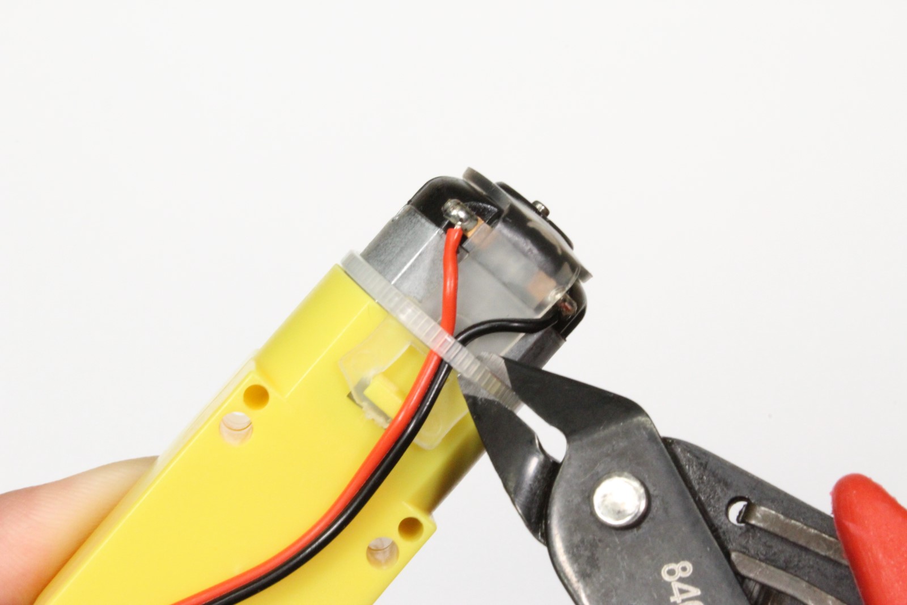
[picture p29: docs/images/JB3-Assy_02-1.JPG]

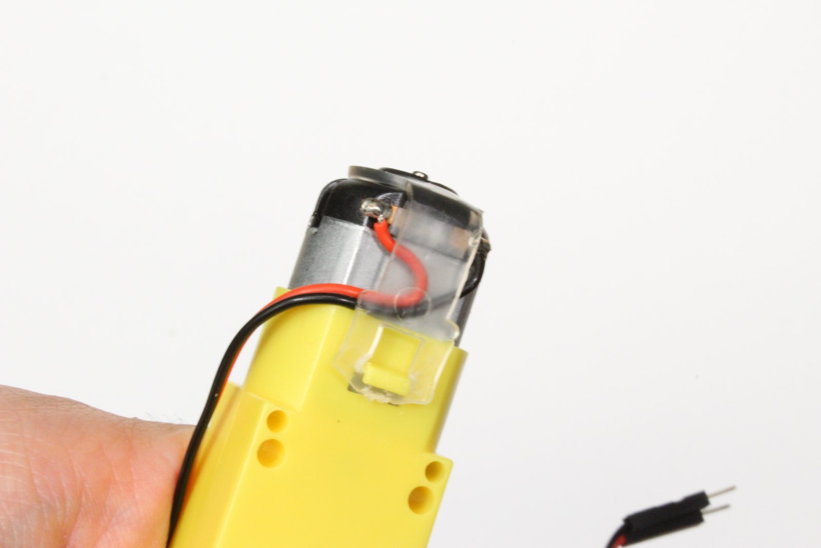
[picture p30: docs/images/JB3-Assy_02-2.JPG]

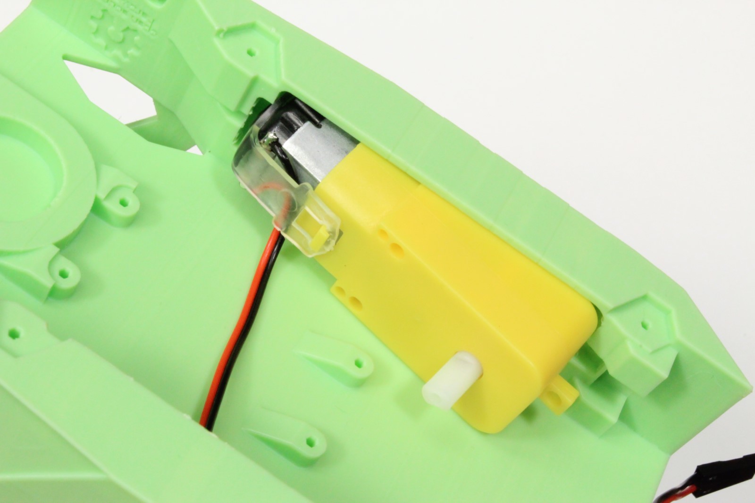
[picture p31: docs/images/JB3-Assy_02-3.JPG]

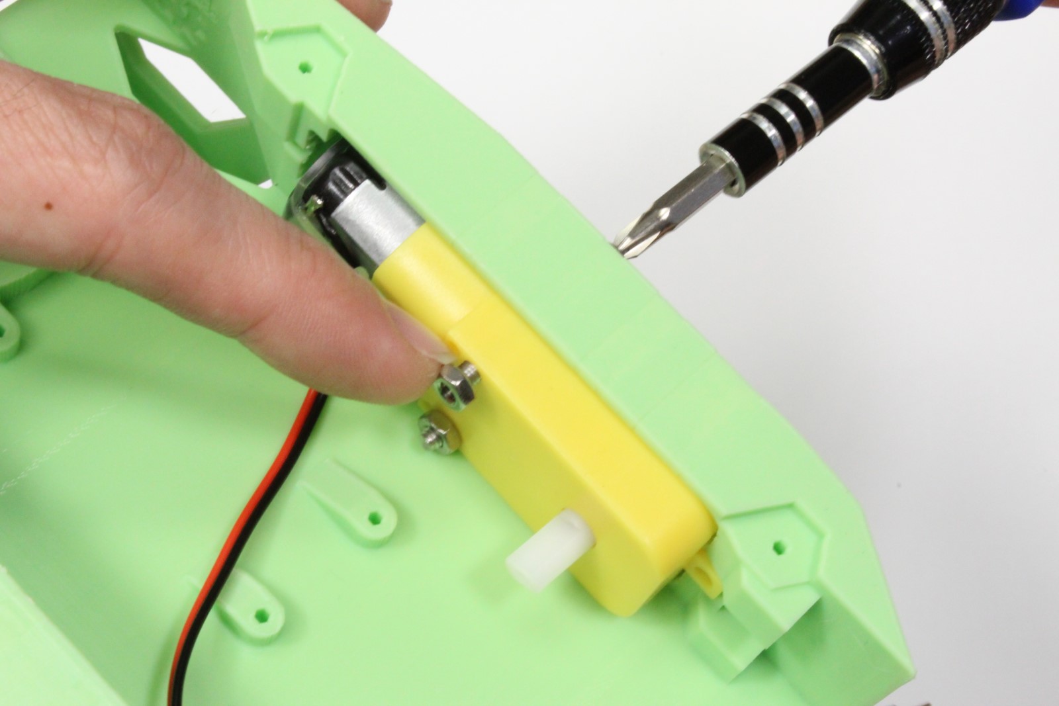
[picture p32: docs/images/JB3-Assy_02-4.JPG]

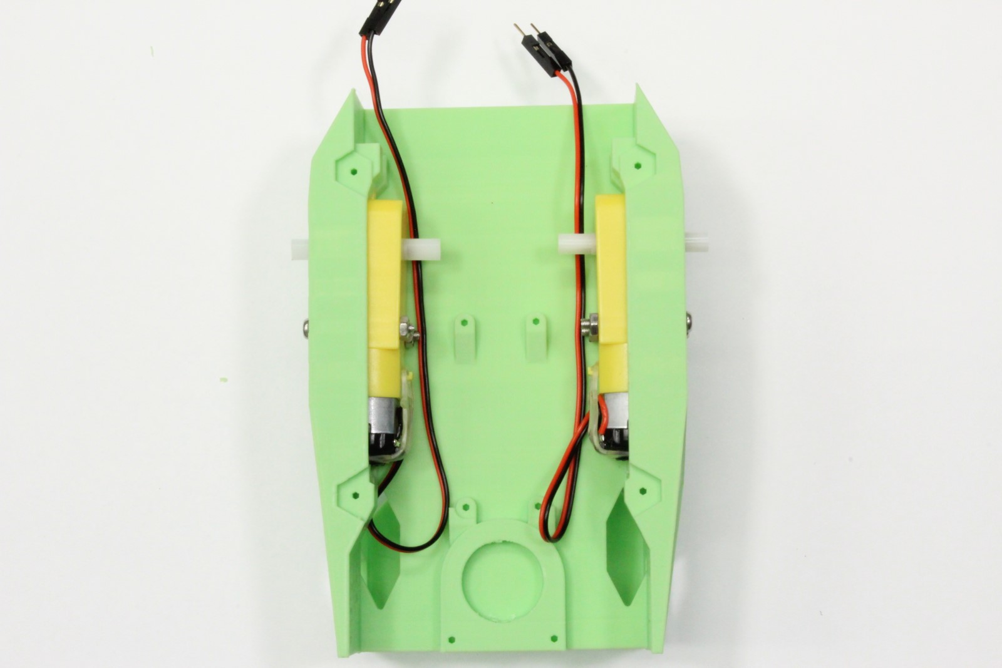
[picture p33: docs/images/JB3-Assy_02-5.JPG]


1. Cut and remove the zip tie from each motor

2. Tuck the wires beneath transparent band to prevent stress on solder joints
3. Insert each motor into the 3D printed chassis
4. Secure each motor with 2x M3x25mm screws

### Step 3 - Solder motor driver

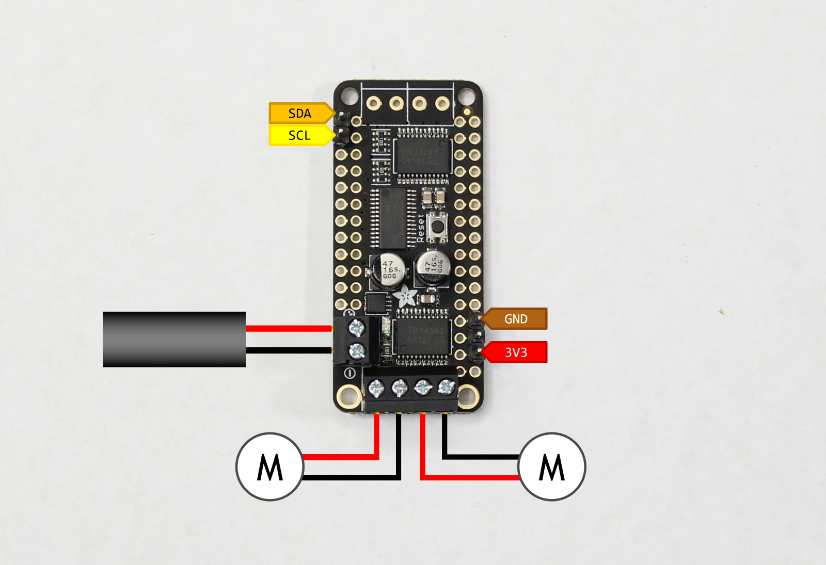
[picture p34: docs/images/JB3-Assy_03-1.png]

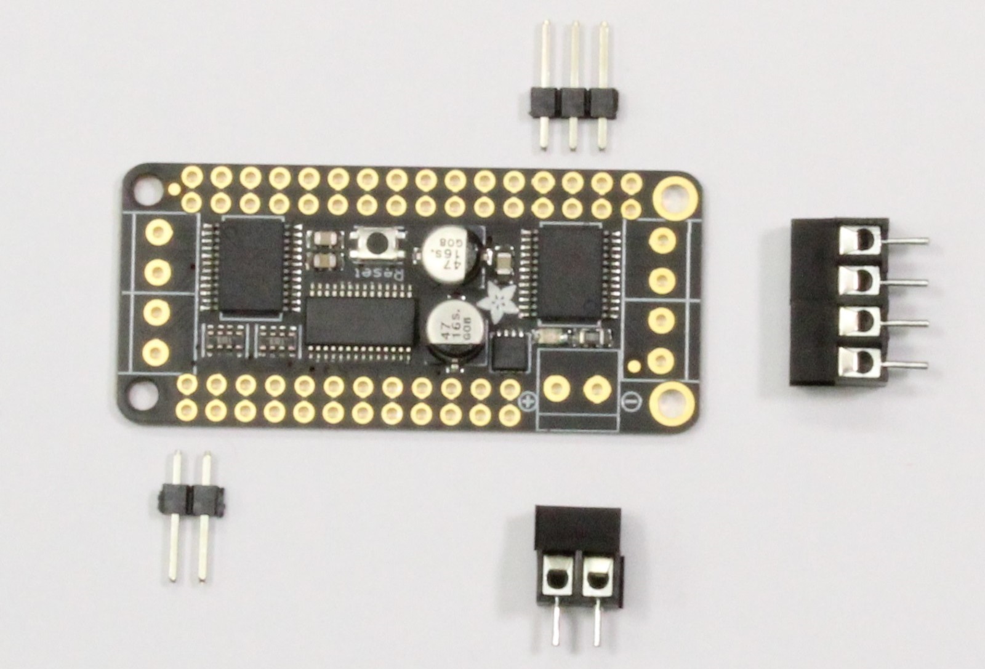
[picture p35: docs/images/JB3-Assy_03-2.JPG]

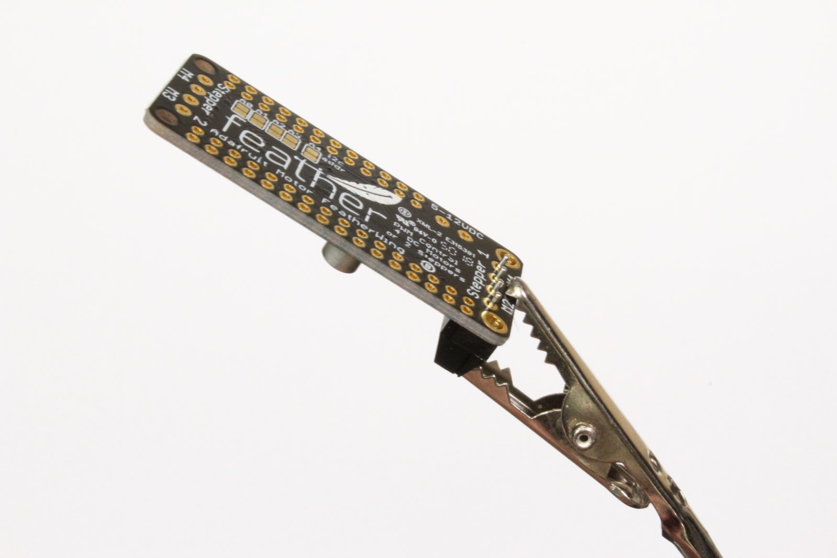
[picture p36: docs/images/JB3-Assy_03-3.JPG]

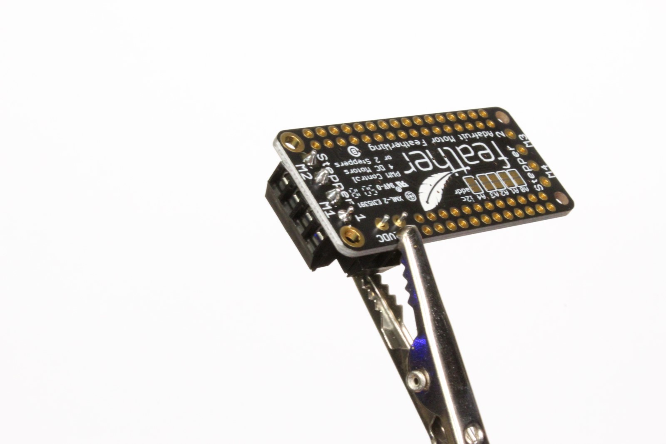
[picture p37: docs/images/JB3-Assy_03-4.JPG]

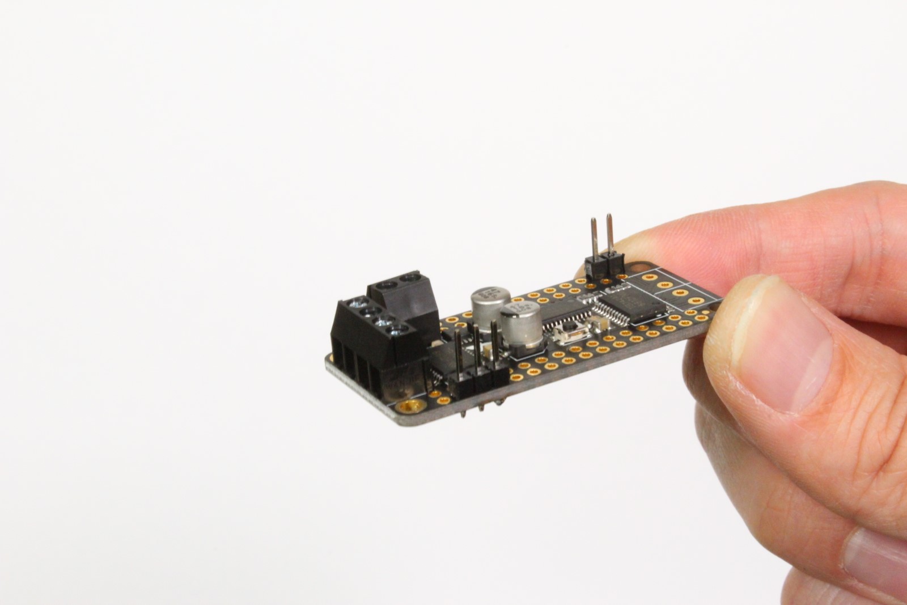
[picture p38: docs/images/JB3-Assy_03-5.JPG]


1. Break away 3-pin and 2-pin male headers from header link that comes with motor driver package

2. Join two of the screw terminal blocks to create a 4-pin screw terminal
3. Solder the 2-pin and 4-pin screw terminals to motor driver
4. Solder the 2-pin and 3-pin male headers to motor driver

    ???+ warning  
        Pay careful attention to the position of the 3-pin header.  It is offset by 1-pin from the corner.

### Step 4 - Strip motor driver power cable

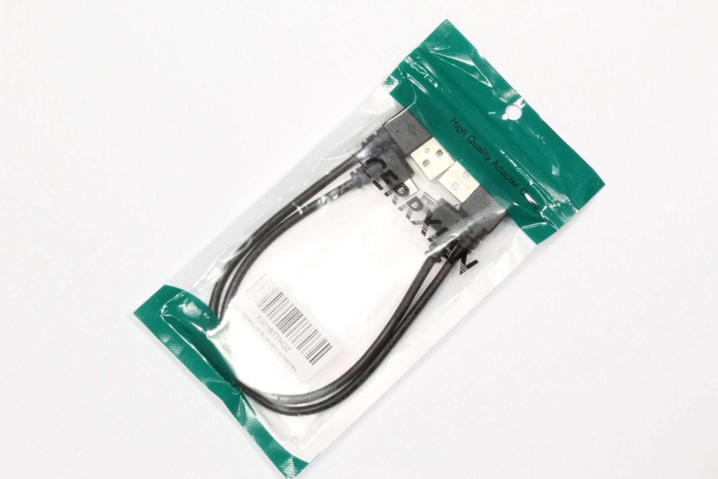
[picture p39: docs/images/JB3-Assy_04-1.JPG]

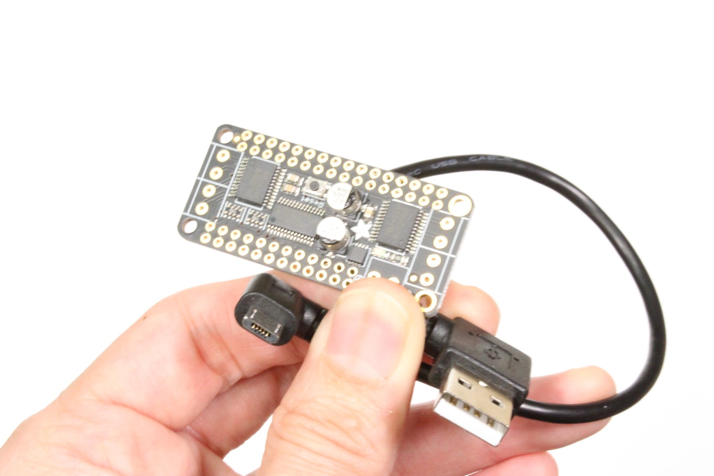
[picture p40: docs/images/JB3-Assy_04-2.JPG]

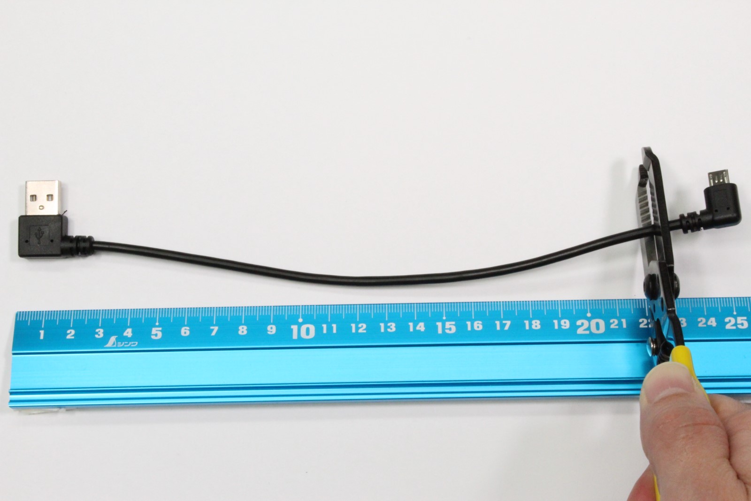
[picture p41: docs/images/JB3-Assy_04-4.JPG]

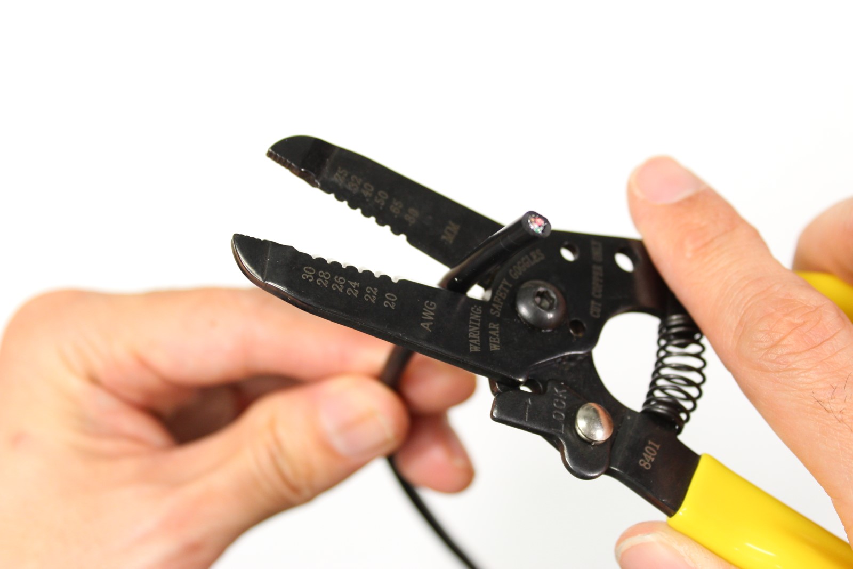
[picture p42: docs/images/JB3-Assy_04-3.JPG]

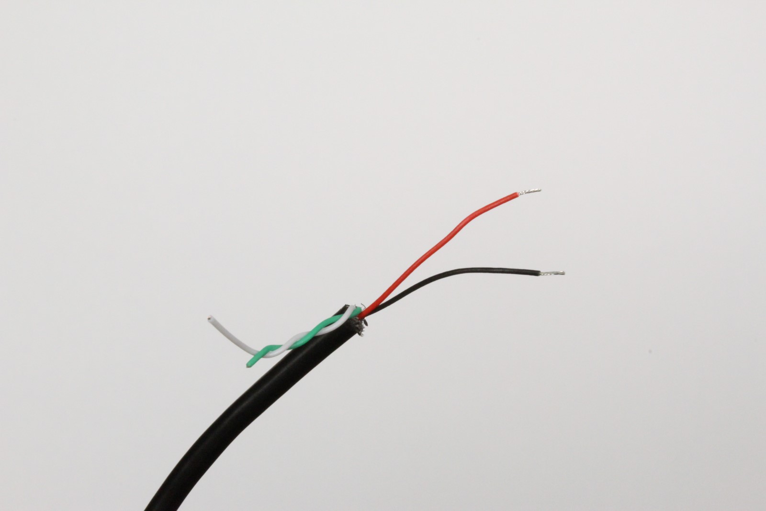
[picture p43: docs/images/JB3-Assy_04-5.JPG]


1. Select the depicted micro USB from the pack 

    ???+ warning
        Pay careful attention to the image.  The cables are not identical.  
        The other micro USB cable will be used to power the Jetson Nano.  Using the wrong power cable for Nano will block it's Ethernet port.

2. Cut the depicted cable roughly ~20cm from the type-A terminal
2. Strip the rubber coating ~3cm from the cut
3. Remove the green / white wires and metal shielding.
4. Strip the red and black wires about ~5mm from cut
5. (optional) Twist the exposed strand wire and coat with solder

### Step 5 - Mount motor driver 

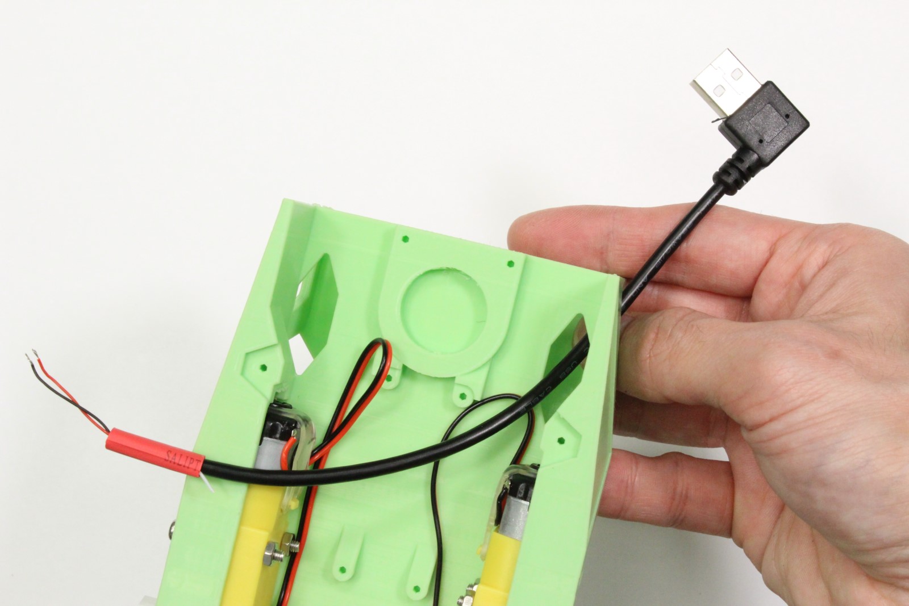
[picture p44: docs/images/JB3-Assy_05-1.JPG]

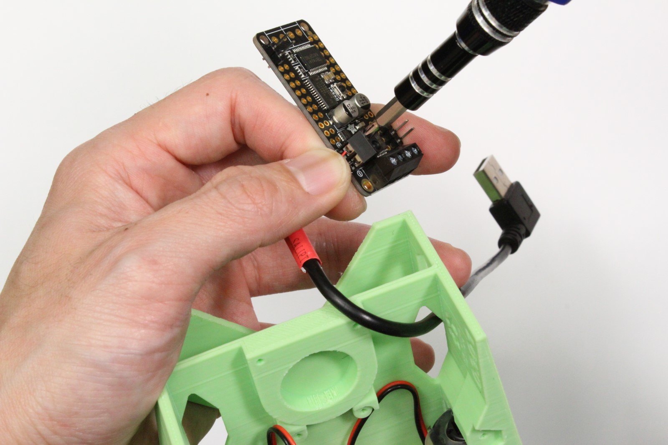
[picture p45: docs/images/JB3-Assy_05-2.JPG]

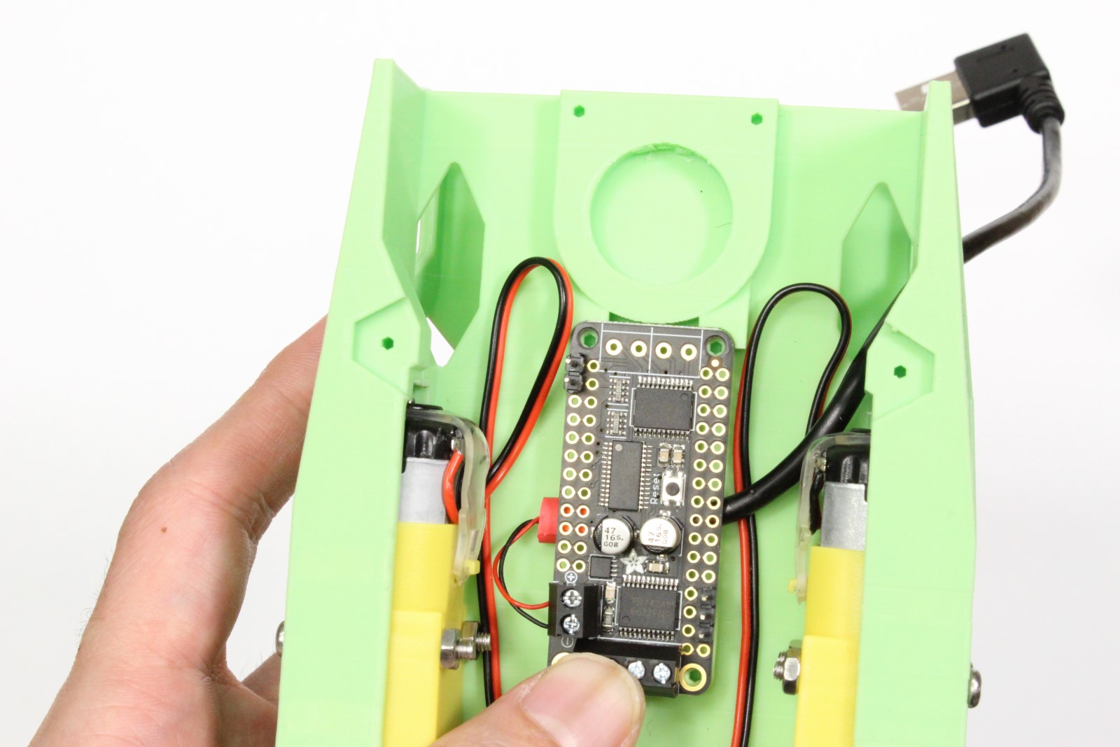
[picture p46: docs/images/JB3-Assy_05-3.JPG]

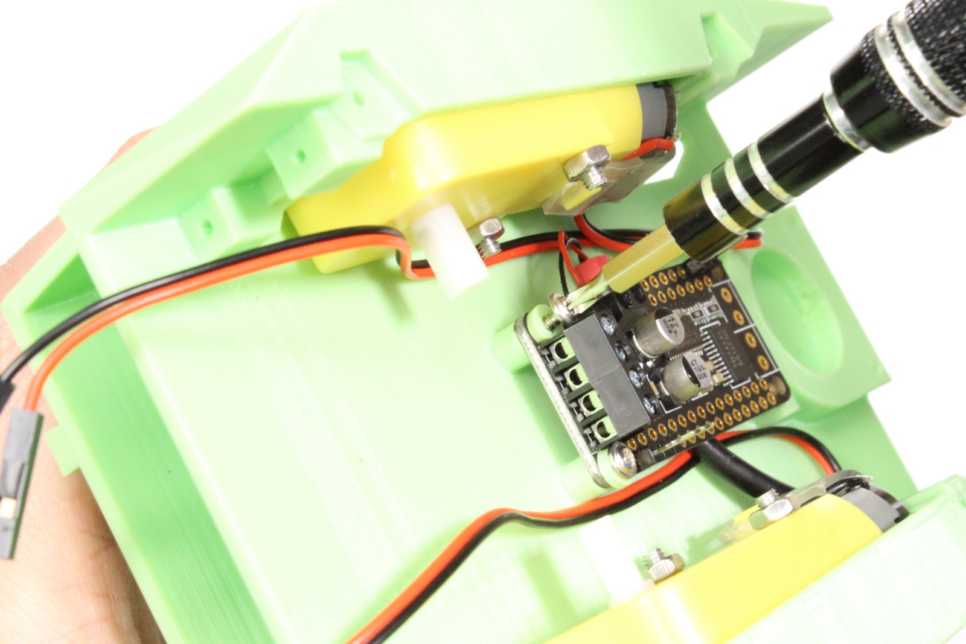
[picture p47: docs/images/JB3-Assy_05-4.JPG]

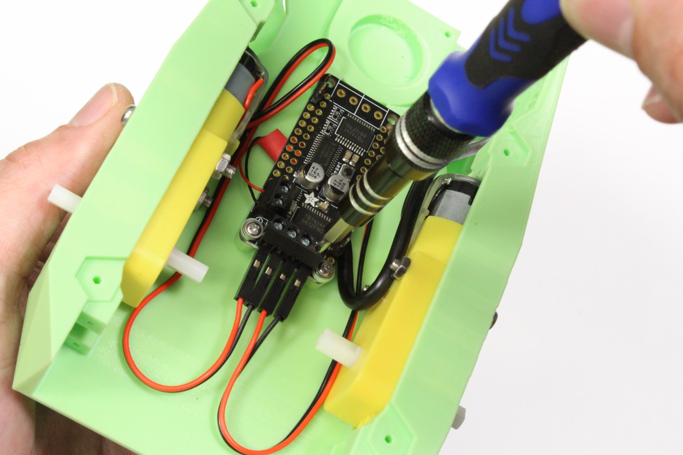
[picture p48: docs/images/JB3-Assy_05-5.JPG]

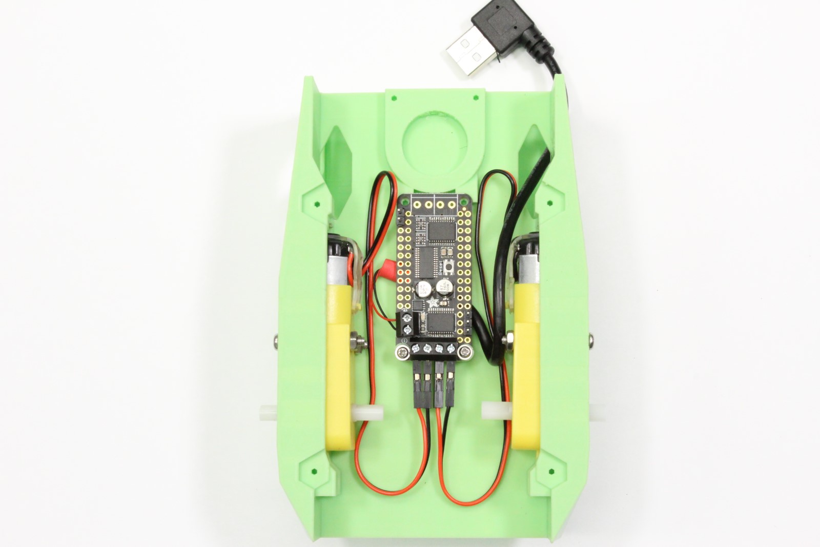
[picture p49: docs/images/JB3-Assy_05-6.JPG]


1. Route the spliced cable through chassis

2. Secure exposed red (+) and black (-) wires to the power terminals on motor driver

    ???+ warning
        Pay attention to the markings on the motor driver.  Incorrect wiring could damage the driver.

3. Route the spliced cable under the motor driver to organize and prevent stress on screw terminal
4. Secure motor driver to chassis using self taping screws
5. Secure left and right motor wires to motor screw terminals

    ???+ info
        ***Notice (3/11/2019):*** We made a slight mistake: the red and black wires for the left and right motor are actually flipped in the image shown above.  This will not cause damage, but the motors will spin backwards.  Please flip them to the correct orientation.

### Step 6 - Mount WiFi antennas

!!! attention ""

    Skip this step if you are using a USB WiFi dongle instead of the M.2 WiFi module

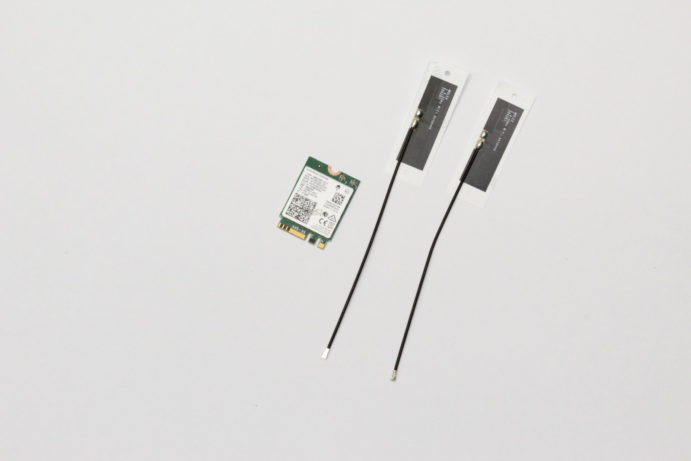
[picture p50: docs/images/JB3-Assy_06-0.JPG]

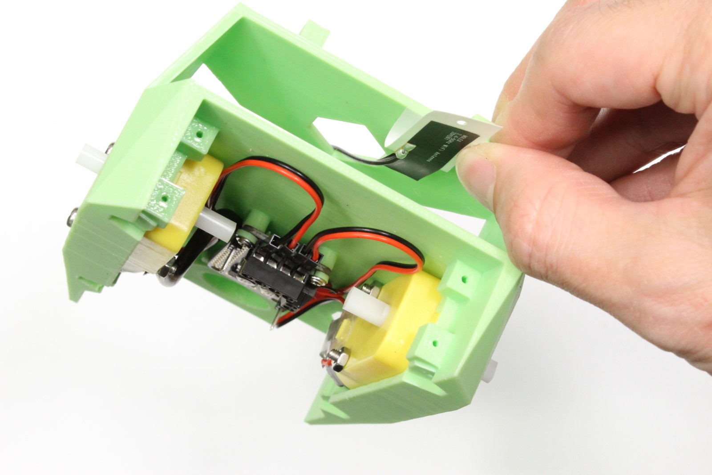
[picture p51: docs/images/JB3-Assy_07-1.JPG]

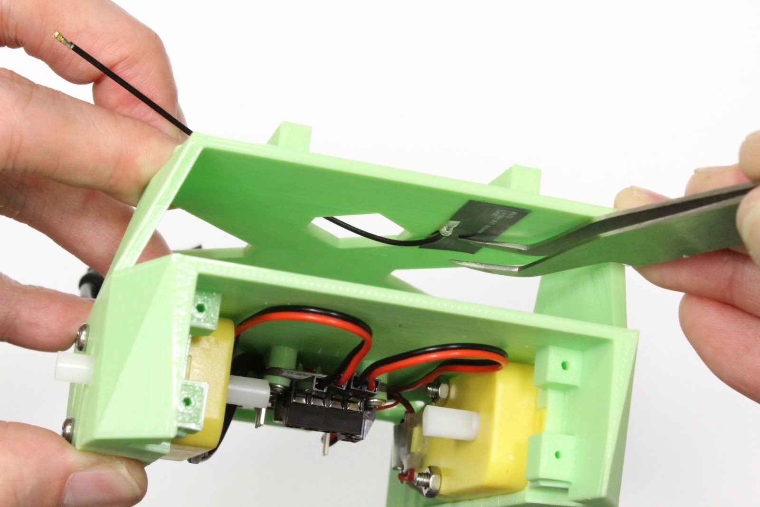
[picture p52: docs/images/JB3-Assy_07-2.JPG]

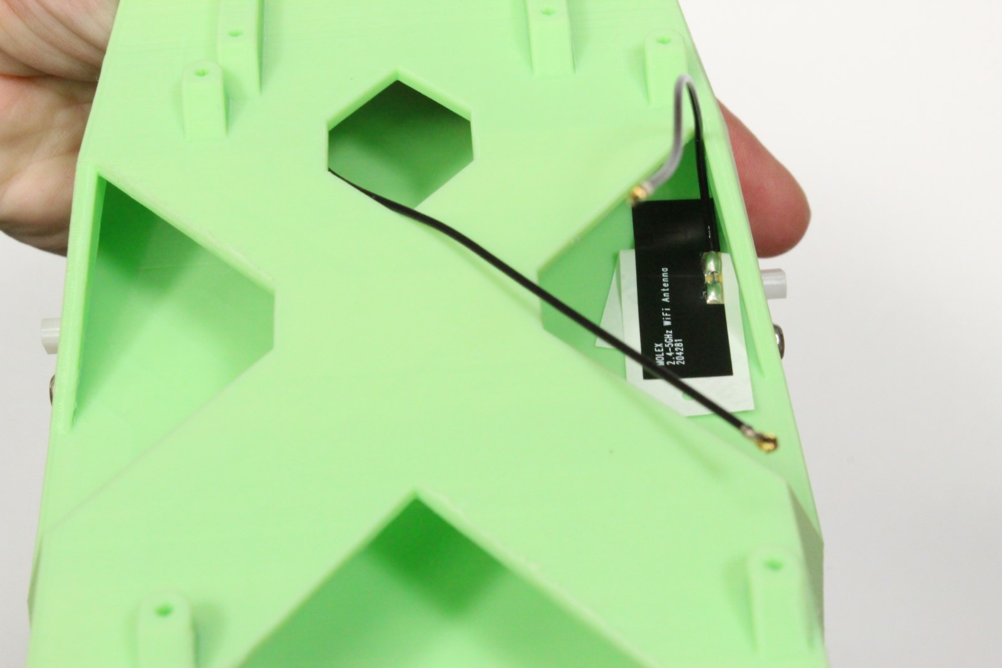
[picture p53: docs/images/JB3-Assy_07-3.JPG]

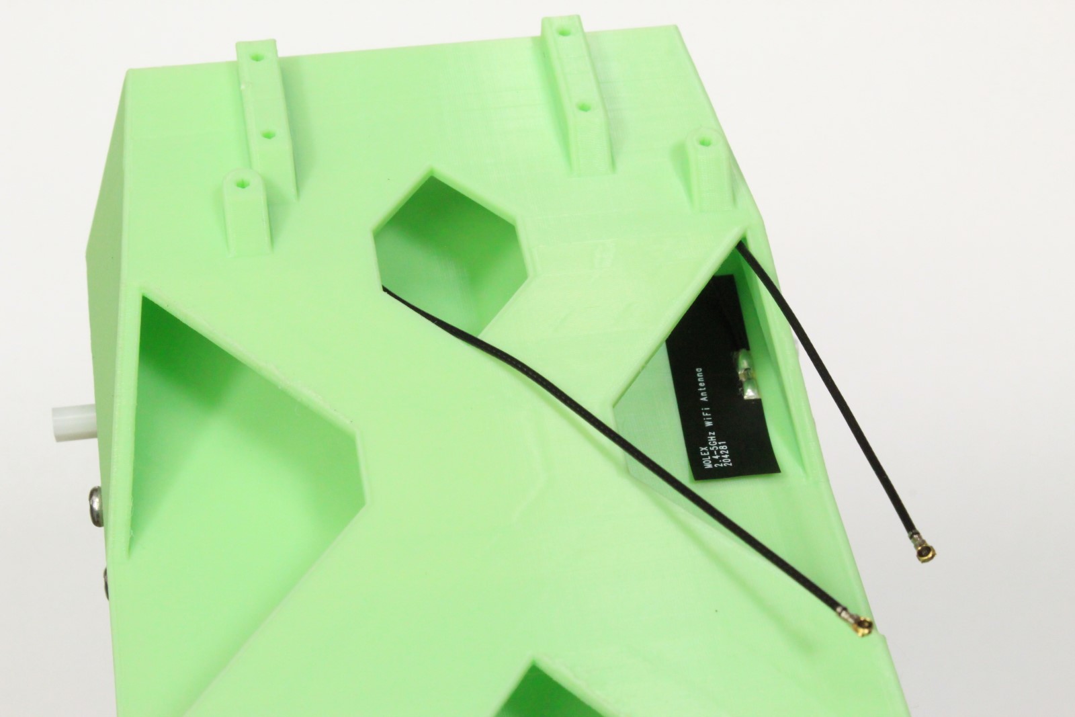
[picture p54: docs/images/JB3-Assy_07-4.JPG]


1. Secure one patch antenna to the underside of top plate

2. Secure the other patch antenna at edge of battery bay
3. Route connectors as shown

### Step 7 - Remove Jetson Nano module from developer kit

!!! attention ""

    Skip this step if you are using a USB WiFi dongle instead of the M.2 WiFi module

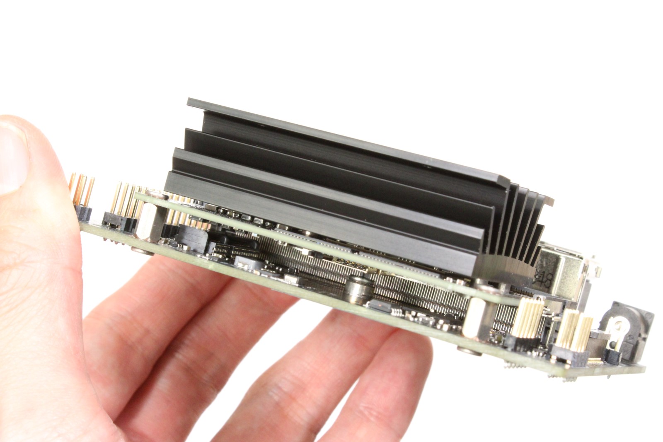
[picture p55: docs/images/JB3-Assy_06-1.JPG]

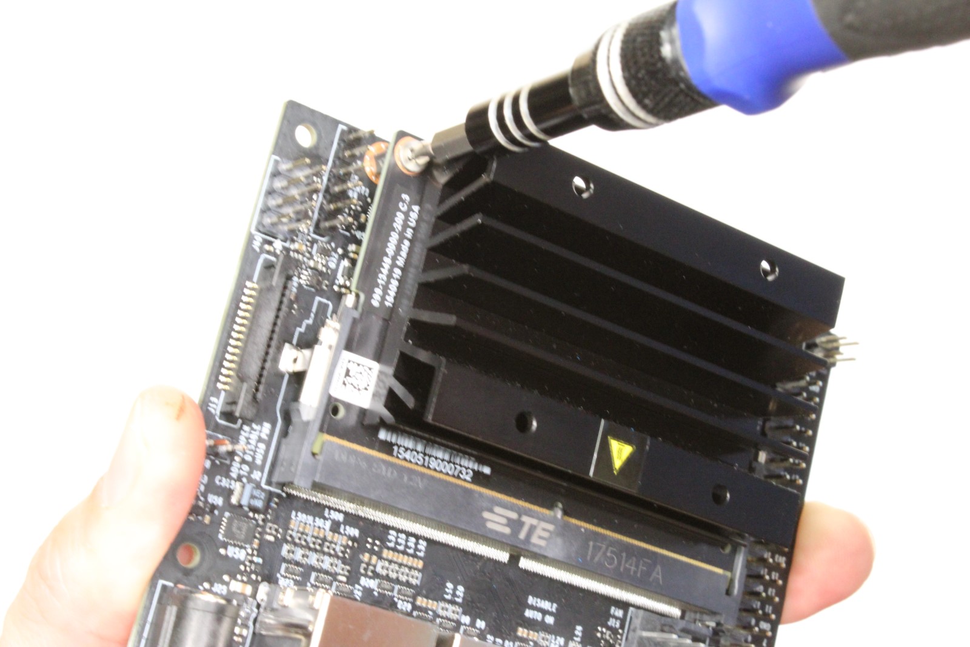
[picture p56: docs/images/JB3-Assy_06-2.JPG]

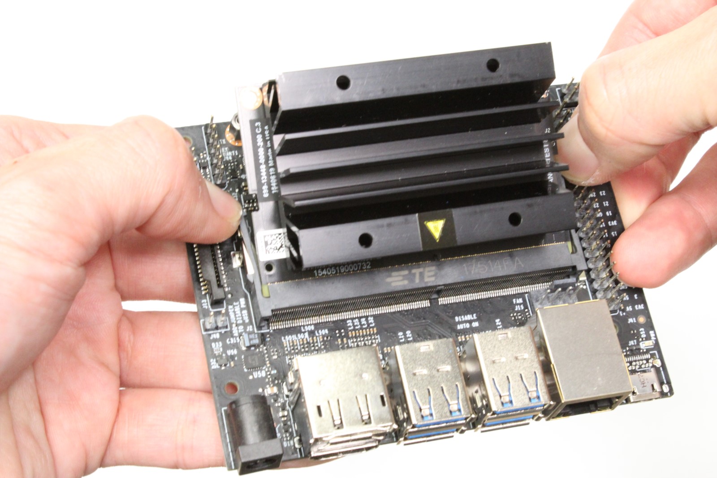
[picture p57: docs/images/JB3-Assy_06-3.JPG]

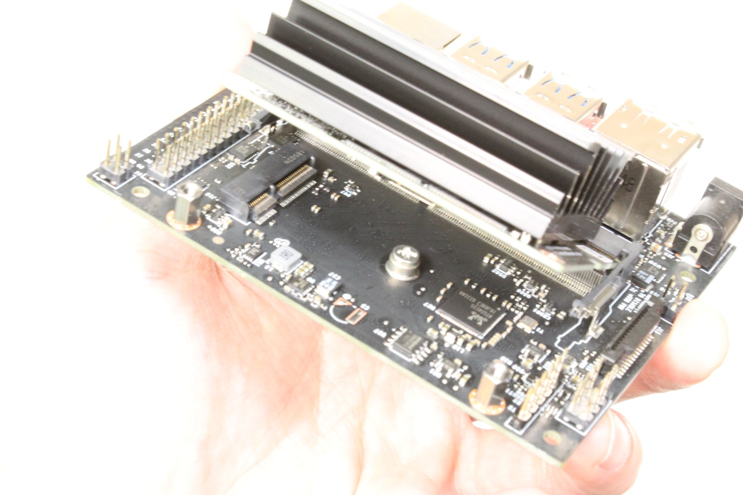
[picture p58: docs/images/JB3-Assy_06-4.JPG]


1. Remove standoff screws from Jetson Nano module

2. Release the side latches of SODIMM connector using hands
3. Slide Jetson Nano module out of SODIMM connector

### Step 8 - Attach WiFi module to developer kit

!!! attention ""

    Skip this step if you are using a USB WiFi dongle instead of the M.2 WiFi module








1. Attach developer kit to chassis using self taping screws

2. Snap antennae on to WiFi module using fingers
3. Remove the screw from developer kit by the M.2 socket
4. Insert WiFi module into M.2 slot on developer kit
5. Fasten WiFi module to developer kit with screw removed in (3)
6. Re-attach the Jetson Nano module to developer kit

### Step 9 - Mount ball caster






1. Place the caster ball inside of shroud

2. Insert the caster base into shroud, securing the ball

    ???+ tip 
        Depending on how the print turns out, the ball socket enclosure may fit too tight. If this is the case, you can easily use a file to remove some excess material.

3. Attach the assembled caster onto the chassis with self taping screws

### Step 10 - Solder header onto *PiOLED* display




1. Secure the 6-pin right angle header to PiOLED display by some method

2. Solder the pins depicted (3.3V, SDA, SCL, and GND solder seen when zoomed in on right image)

    ???+ warning
        The pins are close to the display screen, be careful to avoid the screen with soldering iron tip. 

### Step 11 - Wire motor driver to *PiOLED* display





1. Select 4 wire segment of female-female jumper cables.

    ???+ info
        We use brown, red, orange, yellow segment.  You can map the colors accordingly.

2. Attach 3.3V (red), GND (brown), SDA (orange), and SCL (yellow) to motor driver as shown
3. Route the 4 wire jumper cable segment through chassis
4. Attach red, brown, orange and yellow wires to right angle header as depicted

    ???+ warning 
        Pay close attention!  Reversing the red / brown wires could damage the system.

### Step 12 - Mount camera






1. Attach the camera to the camera mount using 4x self tapping screws

2. Attach the camera mount to chassis with 4x self tapping screws
3. Insert the other end of ribbon cable into Jetson Nano developer kit
4. (optional) Tuck the ribbon cable against heat sink to organize

### Step 13 - Attach wide angle sensor








1. Peel off the original camera sensor

2. Remove any excess adhesive material
3. Remove the adhesive film cover from wide angle replacement sensor
4. Attach wide angle replacement sensor to camera module
5. Ensure the sensor connector is fastened to camera module

### Step 14 - Mount battery






1. Attach double sided adhesive tabs to each end of battery, leaving some tab exposed

2. Holding robot upside down, slide battery into battery bay
3. Holding the battery in place, flip the robot and secure battery to chassis

### Step 15 - Organize wires





1. Route USB cables through chassis to organize and prevent dragging

## Finished JetBot

Once finished, your JetBot should look similar to this.



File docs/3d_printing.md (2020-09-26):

This page has useful information related to printing the JetBot chassis using a 3D printer.  There are two methods for printing JetBot

* Print by yourself
* Use a printing service

## Method 1 - Print by yourself

If you have a 3D printer, we recommend printing the JetBot components yourself!

### Print facts

Below are some facts related to printing a single JetBot.

* Print time:  10-12 hours
* Material used:  < 100 grams
* Material cost:  ~ $2

### Tested Printers

We've tested that the following printers are able to print JetBot successfully.

| Model | Cost | URL |
|---|---|---|
| Monoprice Voxel | $320 | [Amazon](https://amzn.to/2GbUJ5Q) |
| Ultimaker 2+ | $2500 | [Amazon](https://amzn.to/2t8UDU0) |

### Tested Filaments

Based on our experience, we recommend using PLA filament when printing JetBot.  Below is a collection
of filaments that we have tested with the [Monoprice Voxel](https://amzn.to/2GbUJ5Q) 3D printer.

| Brand | Thickness | Material | Color | URL | Notes |
|---|---|---|---|-----|---|
| AmazonBasics | 1.75mm | PLA | Silver | [Amazon](https://amzn.to/2BkrKZP) | Smooth, dark metallic finish |
| AmazonBasics | 1.75mm | PLA | Neon Green | [Amazon](https://amzn.to/2HPg1YR) | Smooth, pale finish|
| AmazonBasics | 1.75mm | PLA | Yellow | [Amazon](http://amzn.com/B07D6CPFP4/) | Bold yellow, slightly translucent |
| AmazonBasics | 1.75mm | PLA | Purple | [Amazon](#) | Smooth, pale finish |

### Printing and slicing configuration

* STL unit: **mm**

* Print orientation



* Slice configuration (Cura)



## Method 2 - Use a printing service

If you don't have a 3D printer on hand, and are not interested in purchasing one, there are external services
that can print the chassis for you.  Below are some quotes from popular 3D printing services

> Please note, we have not tested these services yet ourselves, so please proceed with caution.  If you
> find a print service that worked well for you, we'd love to hear!  Please let us know by creating
> an issue on GitHub or mentioning it in the chat channel

| Service | Quote |
|---|---|
| [3DHubs](https://www.3dhubs.com/) | $36.66 |
| [Jinxbot](https://jinxbot.com/) | $91.42 |
| [Sculpteo](https://www.sculpteo.com/) | ~$100 |

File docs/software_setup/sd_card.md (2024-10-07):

# Software Setup (SD Card Image)

!!! note

    JetBot was originally designed with ***Jetson Nano Developer Kit***, which was [discontinued](https://forums.developer.nvidia.com/t/jetson-nano-developer-kit-eol/276729).

    For those newly starting, we recommend planning the JetBot assembly with **Jetson Orin Nano 8GB Developer Kit**.<br>
    The Bill of Materials for Orin version of JetBot is laid out on [Bill of Materials (Orin)](./bill_of_materials_orin.md) page.

    Please note that, currently, the software for the Orin version of JetBot is still work in progress.

This page details how to set up JetBot using the pre-built JetBot SD card image. You may prefer this option if you are new to Jetson Nano, and do not have an existing SD card configured.

## Step 1 - Download the pre-built JetBot SD card image

Download the pre-built JetBot SD card image from the table below.  Make sure to select the version that matches the Jetson you're using  (for example Jetson Nano 2GB).

!!! Success "Good News"

    10/7/2024:

    The JetBot image files have been successfully moved to a different server and are now available again.

    If you experienced any issues accessing the files over the past two weeks, please try downloading them again.

### Latest Release

| Platform | JetPack Version | JetBot Version | Download | MD5 Checksum | 
|---|---|---|---|----|
| Jetson Nano 2GB | 4.5 | 0.4.3 | [jetbot-043_nano-2gb-jp45.zip](https://nvidia.box.com/shared/static/4su20xg3w0mtvna99jr21m8ix80jhe5y.zip) | e6dda4d13b1b1b31f648402b9b742152 |
| Jetson Nano (4GB) | 4.5 | 0.4.3 | [jetbot-043_nano-4gb-jp45.zip](https://nvidia.box.com/shared/static/mhtefkijy2c267rbuux6mhelj7ynjohz.zip) | 760b1885646bfad8590633acca014289 |

???+ attention
    To use one of the JetBot sdcard images based on JetPack 4.5, you first need to boot your Jetson Nano using a plain JetPack 4.5 SD card image and run through the operating system setup.
    This will perform a one-time configuration which enables you to use SD card images based on JetPack 4.5 on your device.  You can find the original JetPack SD card images
    here: [JetPack SD card image for Jetson Nano 2GB](https://developer.nvidia.com/jetson-nano-2gb-sd-card-image) and [JetPack SD card image for Jetson Nano (4GB)](https://developer.nvidia.com/jetson-nano-sd-card-image).  After doing this procedure once, you can then use the JetPack 4.5 based JetBot SD card images listed above on your device.

### Old releases

| Platform | JetPack Version | JetBot Version | Download |
|---|---|---|---|
| Jetson Nano (4GB) | 4.2 | 0.3.2 | [jetbot_image_v0p3p2.zip](https://nvidia.box.com/shared/static/fh612qv6d9h5hqfpihczddnhio1i8j7d.zip) | 

<!-- | Jetson Nano 2GB | 4.4.1 | 0.4.2 | [jetbot-042_nano-2gb-jp441.zip](https://drive.google.com/file/d/1uiWz6QTcqB3wzN81gdv_zY8t_V3ZzkNE/view) |
| Jetson Nano (4GB) | 4.4.1 | 0.4.2 | [jetbot-042_nano-4gb-jp441.zip](https://drive.google.com/file/d/1MAX1ibJvcLulKQeMtxbjMhsrOevBfUJd/view) |
| Jetson Nano 2GB | 4.4.1 | 0.4.1 | [jetbot-041_nano-2gb-jp441.zip](https://drive.google.com/file/d/1d03TOrQyffxFsv_Nhp-XQ7Q3-nCHbT9a/view) |
| Jetson Nano (4GB) | 4.4.1 | 0.4.1 | [jetbot-041_nano-4gb-jp441.zip](https://drive.google.com/file/d/1yQ5MEiiBxbytCXHFPPBi-5SAxWklhZQA/view) |
| Jetson Nano (4GB) | 4.3 | 0.4.0 | [jetbot_image_v0p4p0.zip](https://drive.google.com/open?id=1G5nw0o3Q6E08xZM99ZfzQAe7-qAXxzHN) | -->

## Step 2 - Flash JetBot image onto SD card

1. Insert an SD card into your desktop machine

3. Using [Etcher](https://www.balena.io/etcher/), select the image you downloaded above and flash it onto the SD card.

4. Remove the SD card from your desktop machine

## Step 3 - Boot Jetson Nano

1. Insert the SD card into your Jetson Nano (the micro SD card slot is located 
   under the module)

2. Connect the monitor, keyboard, and mouse to the Nano
3. Power on the Jetson Nano by connecting the micro USB (for Jetson Nano (4GB)) or USB-C (for Jetson Nano 2GB) charger to the port

    ???+ attention 
        We recommend first booting the Jetson Nano once without the piOLED / motor driver connected.

        This way you can check to make sure the system boots properly from the SD card image without worrying about hardware issues.  After you've verified that it boots, reconnect the piOLED, double check your wiring, and boot again.

## Step 4 - Connect JetBot to WiFi

Next you'll need to connect to WiFi.  To reduce memory consumption, we disable the Ubuntu GUI in the latest JetBot SD card image.  For this reason, you'll need to use the command line to connect to WiFi.

1. Log in using the user ``jetbot`` and password ``jetbot``
    
2. Connect to a WiFi network using the following command

    ```bash
    sudo nmcli device wifi connect <SSID> password <PASSWORD>
    ```
    
Your Jetson Nano should now automatically connect to the WiFi at boot and display it's IP address on the piOLED display.

???+ tip
    If you're having trouble figuring out how to get connected to Wi-Fi, check out the [Wi-Fi setup](wifi_setup.md) page for more detailed instructions 

## Step 5 - Connect to JetBot from web browser

After your robot is connected to WiFi, you no longer need to have the robot connected by a monitor.  You can connect to the robot from your laptop's web browser by performing the following steps

1. Shutdown JetBot using the command line

    ```bash
    sudo shutdown now
    ```

2. Unplug your HDMI monitor, USB keyboard, mouse and power supply from Jetson Nano

3. Power the JetBot from the USB battery pack by plugging in the micro-USB cable
4. Wait a bit for JetBot to boot
2. Check the IP address of your robot on the *piOLED* display screen.  Enter this in place of ``<jetbot_ip_address>`` in the next command
3. Navigate to ``http://<jetbot_ip_address>:8888`` from your desktop's web browser. You can do this from any machine on your local network.  
4. Sign in using the password ``jetbot``.

That's it, you've now accessed JetBot's remote programming environment! 

You will be presented with a view similar to the following. 



Here you can easily access the JetBot examples!  From this point on, when you power on the JetBot, it should automatically connect to WiFi and display it's IP address.  So all you need to do is reconnect using your web browser to start programming!

Now that you're finished setting up your JetBot, you're ready to run the [examples](../examples/basic_motion.md).

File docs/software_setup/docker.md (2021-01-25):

# Software Setup (Docker)

This page details how to set up JetBot using the pre-built JetBot docker containers. This is the best option if you want to use JetBot with an existing Jetson Nano SD card image.

???+ note
    Please note, the JetBot containers described in this page currently target a Jetson Nano SD card image flashed with JetPack 4.4. These containers will not work with other version of JetPack.

## Step 1 - Setup Jetson Nano

If you haven't already, go through the initial setup of Jetson Nano.<br>
You can use your existing Jetson Nano set up (microSD card), as long as you have enough storage space left.

???+ hint
    For this, we'll assume you've set up your Jetson Nano using the **online Getting Started guide**.
        
     - [Getting Started With Jetson Nano Developer Kit](https://developer.nvidia.com/embedded/learn/get-started-jetson-nano-devkit)
     - [Getting Started with Jetson Nano 2GB Developer Kit](https://developer.nvidia.com/embedded/learn/get-started-jetson-nano-2gb-devkit)

## Step 2 - Connect to Wi-Fi

If you haven't already, connect your Jetson Nano to your Wi-Fi network.

Follow this [Wi-Fi setup](wifi_setup.md) guide.

## Step 3 - Clone JetBot repo

Clone the [official JetBot GitHub repo](https://github.com/NVIDIA-AI-IOT/jetbot).

```bash
git clone http://github.com/NVIDIA-AI-IOT/jetbot.git
```

## Step 4 - Configure System

First, call the [``scripts/configure_jetson.sh``](https://github.com/NVIDIA-AI-IOT/jetbot/blob/master/scripts/configure_jetson.sh) script to configure the power mode and other parameters.

```bash
cd jetbot
./scripts/configure_jetson.sh
```

???+ hint
    `configure_jetson.sh` also disables the GUI for the interest of saving system memory (DRAM) consumption.<br>
    If you want to re-enable the GUI, you can execute the following command.
    
    ```bash
    sudo systemctl set-default graphical.target
    ```
    
    Optionally, you can execute this script (`./scripts/re_enable_gui.sh`). 

Then, call the [``scripts/enable_swap.sh``](https://github.com/NVIDIA-AI-IOT/jetbot/blob/master/scripts/enable_swap.sh) script to enable swap memory if not set.<br>
Having extra 4GB swap memory is recommended even on Jetson Nano (4GB) Developer Kit.

```bash
./scripts/enable_swap.sh
```

## Step 5 - Enable all containers

Call the following to enable the JetBot docker containers 

```bash
cd docker
./enable.sh $HOME   # we'll use home directory as working directory, set this as you please.
```

Now you can go to ``https://<jetbot_ip>:8888`` from a web browser and start programming JetBot!

You can do this from any machine on your local network.  The password to log in is ``jetbot``.



The `enable.sh` script causes the docker containers to restart at boot. This means the next time you power on your JetBot, the containers will automatically start, and you should see the IP address displayed on the PiOLED display screen. All you need to do is type this into your web browser and start programming!

???+ tip
    For more information on configuring and using docker with JetBot, check out the [Docker Tips](../reference/docker_tips.md) page.
    
Now that you've finished setting up you're JetBot, you're ready to run through the [examples](../examples/basic_motion.md)!

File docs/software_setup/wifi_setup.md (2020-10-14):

# Wi-Fi connection setup 

???+ info
    You can skip this page if you already have a wireless connection to your JetBot from your computer.

To go through the actual example applications on JetBot, you interact with JetBot from your (laptop) PC through Wi-Fi network.

This document explains how you can initially set up the Wi-Fi connection on your Jetson.

## Monitor-attached Mode

The easiest way to set up the Wi-Fi connection on your Jetson, is to operate on the GUI desktop.<br>
For this you need to fisrt connect the following to the Jetson on your JetBot.

- HDMI monitor
- USB keyboard
- USB mouse

With this setup, you can use Jetson like a standard Linux computer. <br>
We call this **Monitor-attached Mode**.

???+ hint
    If you don't have above items handy, then you can also try the headless way of configuring Wi-Fi.
    Head down to the next section, [Headless Mode](#headless-mode).

### Connect to Wi-Fi AP

If a Wi-Fi adaptor (either Intel 8265 M.2 card or a USB Wi-Fi dongle) is attached, you can configure the wireless network from the desktop.



### Check IP address

After the connection established, check the IP address.



Note this IP address.



### Verify the IP address

To test the IP address is valid and your Jetson is accesible, try connecting to the IP address from your separate (laptop) PC.

SSH server is enabled by default on Jetson.<br>
Open your SSH client software (PuTTY, etc) on your PC, and try to connect the SSH server on the IP address.



This is how you connect to your JetBot using SSH client software.<br>
Once you confirm you can connect to your Jetson remotely from your PC via Wi-Fi, **you can now remove the HDMI monitor, keyboard and mouse from Jetson**, and let your JetBot free!

And at this point, you are now using Jetson effectively in the Headless Mode.

??? hint
    Alternatively, even on the GUI deskop, you can open the terminal by pressing `Ctrl` + `Alt` + `T` keys, and follow the command-line based setup described below for headless setup.

    

## Headless Mode

When you put your Jetson in a deployed system, like a mobile robot, it is often difficult to attach an HDMI monitor.<br>
We can still control such Jetson remotely through network from a (laptop) PC, ***WHEN you already know the IP address***.<br>
We call this operation mode **Headless Mode**.

However you face a chiken-or-egg dillemna here, because you want to remotely login to the console to set up a Wi-Fi connection, but to do that you first need the IP address of your Jetson that you get after establishing the Wi-Fi connecton.

### USB Device Mode

What comes handy here is **USB Device Mode**.

You connect your (laptop) PC and Jetson using a Micro-USB cable. (Type-A end goes to your PC, Micro-B end goes to Jetson)<br>
Using this wired connection, you can access the terminal on Jetson from your (laptop) PC.

With USB Device Mode, Jetson presents 3 different USB Device Class end-points to the PC that it got connected to.<br>
They function as

- USB mass storage device (you see `L4T-README` drive mounted on your PC, like a USB thumbdrive)
- USB serial (like the common "FTDI" USB to serial adapter)
- USB network interface card (like a virtual Ethernet adapter)

With the virtual Ethernet adapter functinality, Jetson forms a virutal local Ethernet network with Jetson being `192.168.55.1` and your PC being `192.168.55.100`.
So you can actually SSH login from your (laptop) PC by specifying `192.168.55.1`, if you have already set up your acount (with username and password).

If you are using Jetson for the first time right after you flash your SD card, then you don't have this user account set up.<br>
In that case, you want to use the USB serial functinality, and use your serial terminal software on your PC to have accesss to the Jetson's serial terminal.

So either way, with a Micro USB cable, you can have an access to Jetson's terminal.

### Connect Wi-Fi using `nmcli` command

If a Wi-Fi adaptor (either Intel 8265 M.2 card or a USB Wi-Fi dongle) is attached, you can configure the wireless network using `nmcli` command.

You can first check if you want a wireless adapter on your system.<br>
Look for `wlan0`.

```bash
$ nmcli device
DEVICE  TYPE      STATE         CONNECTION
l4tbr0  bridge    connected     l4tbr0
wlan0   wifi      disconnected  --
eth0    ethernet  unavailable   --
dummy0  dummy     unmanaged     --
rndis0  ethernet  unmanaged     --
usb0    ethernet  unmanaged     --
lo      loopback  unmanaged     --
``` 

Then you can list all the wirelss networks (SSDI) in the area.

```bash
$ nmcli device wifi list
IN-USE  SSID                           MODE   CHAN  RATE        SIGNAL  BARS  SE
        --                             Infra  6     195 Mbit/s  82      ▂▄▆█  WP
        --                             Infra  6     195 Mbit/s  82      ▂▄▆█  WP
        --                             Infra  6     195 Mbit/s  75      ▂▄▆_  WP
        MY_WIFI_AP                     Infra  6     195 Mbit/s  70      ▂▄▆_  WP
        --                             Infra  6     195 Mbit/s  70      ▂▄▆_  WP
        *********                      Infra  1     405 Mbit/s  64      ▂▄▆_  WP
        ************                   Infra  153   405 Mbit/s  64      ▂▄▆_  WP
...
```



To connect to your wireless network (AP, access point), issue the commands below.

```bash
$ sudo nmcli device wifi connect <MY_WIFI_AP> password <MY_WIFI_PASSWORD>
Device 'wlan0' successfully activated with '2a26d5ca-****-****-****-**************'.
```

### Check IP address

To check your IP address, use `ifconfig`.
Check the `wlan0` part at the very bottom.

```bash
$ ifconfig
dummy0: flags=195<UP,BROADCAST,RUNNING,NOARP>  mtu 1500
        inet6 fe80::d854:8ff:fe87:e631  prefixlen 64  scopeid 0x20<link>
        ether da:54:08:87:e6:31  txqueuelen 1000  (Ethernet)
        RX packets 0  bytes 0 (0.0 B)
        RX errors 0  dropped 0  overruns 0  frame 0
        TX packets 24  bytes 3376 (3.3 KB)
        TX errors 0  dropped 0 overruns 0  carrier 0  collisions 0

l4tbr0: flags=4163<UP,BROADCAST,RUNNING,MULTICAST>  mtu 1500
        inet 192.168.55.1  netmask 255.255.255.0  broadcast 192.168.55.255
        inet6 fe80::1  prefixlen 128  scopeid 0x20<link>
        inet6 fe80::943c:9dff:fe90:eb89  prefixlen 64  scopeid 0x20<link>
        ether 96:3c:9d:90:eb:89  txqueuelen 1000  (Ethernet)
        RX packets 15189  bytes 1343038 (1.3 MB)
        RX errors 0  dropped 0  overruns 0  frame 0
        TX packets 4344  bytes 411009 (411.0 KB)
        TX errors 0  dropped 0 overruns 0  carrier 0  collisions 0

lo: flags=73<UP,LOOPBACK,RUNNING>  mtu 65536
        inet 127.0.0.1  netmask 255.0.0.0
        inet6 ::1  prefixlen 128  scopeid 0x10<host>
        loop  txqueuelen 1  (Local Loopback)
        RX packets 3954  bytes 287737 (287.7 KB)
        RX errors 0  dropped 0  overruns 0  frame 0
        TX packets 3954  bytes 287737 (287.7 KB)
        TX errors 0  dropped 0 overruns 0  carrier 0  collisions 0

rndis0: flags=4163<UP,BROADCAST,RUNNING,MULTICAST>  mtu 1500
        inet6 fe80::943c:9dff:fe90:eb89  prefixlen 64  scopeid 0x20<link>
        ether 96:3c:9d:90:eb:89  txqueuelen 1000  (Ethernet)
        RX packets 15414  bytes 1360470 (1.3 MB)
        RX errors 0  dropped 7  overruns 0  frame 0
        TX packets 4378  bytes 667985 (667.9 KB)
        TX errors 0  dropped 0 overruns 0  carrier 0  collisions 0

usb0: flags=4099<UP,BROADCAST,MULTICAST>  mtu 1500
        ether 96:3c:9d:90:eb:8b  txqueuelen 1000  (Ethernet)
        RX packets 0  bytes 0 (0.0 B)
        RX errors 0  dropped 0  overruns 0  frame 0
        TX packets 0  bytes 0 (0.0 B)
        TX errors 0  dropped 0 overruns 0  carrier 0  collisions 0

wlan0: flags=4163<UP,BROADCAST,RUNNING,MULTICAST>  mtu 1500
        inet 192.168.1.58  netmask 255.255.255.0  broadcast 192.168.1.255
        inet6 fe80::b5a0:c2e3:50bc:29a4  prefixlen 64  scopeid 0x20<link>
        ether b4:4b:d6:23:9a:12  txqueuelen 1000  (Ethernet)
        RX packets 26825  bytes 40675884 (40.6 MB)
        RX errors 0  dropped 32746  overruns 0  frame 0
        TX packets 16406  bytes 1673647 (1.6 MB)
        TX errors 0  dropped 0 overruns 0  carrier 0  collisions 0
```

### Verify the IP address

To test the IP address is valid and your Jetson is accesible, try connecting to the IP address from your separate (laptop) PC under the same network.

Open your SSH client software (PuTTY, etc) on your PC, and try to connect the SSH server using the IP address you obtained on the wireless adapter.



This is how you connect to your JetBot over Wi-Fi.<br>
Once you confirm you can connect to your Jetson remotely from your PC via Wi-Fi, **you can now remove the Micro USB cable** and let your JetBot free!

???+ info
    Next, you move on to either page below.

    - [Software setup using Docker container](docker.md) 
    - [Software setup using SD card image](sd_card.md)
    
    Once your JetBot software is configure, you should see JetBot's IP address on the small OLED display.<br>
    You would only need to come back to this step to re-connect to the network or to find the IP address when your JetBot fails to get the IP address and show the current IP address on the OLED display.

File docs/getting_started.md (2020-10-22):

# Getting Started

## Step 1 - Pick your vehicle!

To get started with JetBot, first pick your vehicle (hardware) you want to make.



For details of NVIDIA-designed open-source JetBot hardware, check [Bill of Materials](bill_of_materials.md) page and [Hardware Setup](hardware_setup.md) page.

To find kits available from third parties, check [Third Party Kits](third_party_kits.md) page.

## Step 2 - Setup your JetBot

After you've decided which vehicle you want to build, you'll need to source the parts and follow the setup instructions. After that, you're ready to move on to the JetBot examples!

JetBot Getting Started Steps

### Option 1 - DIY JetBot Kit

To get started with the DIY open-source JetBot, follow these steps.

1. Get the parts from the [bill of materials](bill_of_materials.md).

2. Follow the [hardware setup](hardware_setup.md)

3. Follow the [software setup](software_setup/sd_card.md)

### Option 2 - Third Party JetBot Kit

Third party JetBot kits may have different setup instructions from the DIY JetBot. To get started with a third party jetbot, we recommend referring to the third party kit's setup instructions for details on how to setup.

Check out the [Third Party Kits](third_party_kits.md) page for links and information related to third party kits.

## Step 3 - Follow the examples

JetBot comes with many examples to teach robotics and AI basics. These give you the experience you need to begin exploring your own applications with JetBot.

### Example 1 - Basic Motion

The [Basic Motion](examples/basic_motion.md) example teaches you how to program JetBot from your web browser with basic motor controls.

### Example 2 - Teleoperation

The [Teleoperation](examples/teleoperation.md) example teaches you how to stream live images from JetBot and control JetBot with a gamepad attached to your laptop.

### Example 3 - Collision Avoidance

The [Collision Avoidance](examples/collision_avoidance.md) example teaches you how to collect data and train a custom Image Classification model to enable JetBot to avoid collisions in a variety of scenarios. The method learned here can be extended to recognize arbitrary classes of image, which can be extended far beyond JetBot!

### Example 4 - Road Following

The [Road Following](examples/road_following.md) example teaches you how to collect data and train a custom Image Regression model to enable JetBot to follow a road. The method learned here can be extended to detect an arbitrary x, y coordinate in an image, which extends far beyond JetBot!

### Example 5 - Object Following

The [Object Following](examples/object_following.md) teaches you how to use a pre-trained object detection model for following an object, like a person, cup, or dog. The pre-trained network you'll learn to use here can be used for a variety of new AI projects.

## And more!

Take the examples, modify them, make JetBot do something new, or create an entirely new AI project of your own.  

If you do something cool with JetBot, [let us know!](https://forums.developer.nvidia.com/c/agx-autonomous-machines/jetson-embedded-systems/jetson-projects)

Happy JetBotting :)

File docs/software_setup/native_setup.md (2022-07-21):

# Native JetBot Setup (without Docker)

This page details how you can configure your Jetson system to use JetBot without Docker.  This is handy when you want to prototype without worrying about docker semantics, or have other reasons to work outside of a docker environment

> If you see any issues with these instructions or have any questions, please feel free to open an issue on github [here](https://github.com/NVIDIA-AI-IOT/jetbot/issues).

## Instructions

### Step 1 - Install dependencies
1. Install NVIDIA JetPack, including NVIDIA TensorRT following [these instructions](https://developer.nvidia.com/embedded/jetpack).
2. Install PyTorch following [this guide](https://forums.developer.nvidia.com/t/pytorch-for-jetson-version-1-11-now-available/72048) provided on the NVIDIA devtalk forums.
3. Install Node JS to support Jupyter Lab

    ```bash
    curl -sL https://deb.nodesource.com/setup_10.x | bash -
    sudo apt-get install -y nodejs libffi-dev
    ```

4. Install Jupyter Lab to support web-programming JetBot

    ```bash
    sudo python3 -m pip install jupyter jupyterlab
    jupyter labextension install @jupyter-widgets/jupyterlab-manager
    ```

5. Install Jupyter Clickable Image widget (to support road following example).
    
    ```bash
    sudo apt-get install -y libssl1.0-dev && \
    git clone https://github.com/jaybdub/jupyter_clickable_image_widget && \
    cd jupyter_clickable_image_widget && \
    git checkout tags/v0.1 && \
    sudo pip3 install -e . && \
    jupyter labextension install js && \
    jupyter lab build
    cd ..
    ```

6. Install other miscellaneous dependencies

    ```bash
    sudo apt-get update && apt-get install -y supervisor unzip
    sudo apt install -y python3-smbus && pip3 install pyzmq
    ```

7. (optional) Install torch2trt to support TensorRT accelerated AI models

    ```bash
    git clone https://github.com/NVIDIA-AI-IOT/torch2trt
    cd torch2trt
    python3 setup.py install
    cd ..
    ```

8. Install the JetBot Python package
    
    ```bash
    git clone https://github.com/NVIDIA-AI-IOT/jetbot
    cd jetbot
    sudo python3 setup.py install
    # if you plan to modify the jetbot python package, call this instead: sudo python3 setup.py develop

    ```

### Step 2 - Set the Jupyter lab password

Call the following from a terminal
```bash
jupyter notebook password
# enter password
```

You could now test the JetBot notebooks by running

```bash
cd jetbot
jupyter lab --ip=0.0.0.0 --no-browser --allow-root
```

and then navigating to ``https://<jetbot_ip>:8888`` and signing in with the password you set.

However, it is convenient to have this server start automatically, which we will detail next.

### Step 3 - Create a system service to start the Jupyter Lab server at boot

1. Create file named ``jetbot_jupyter.service`` and add the following content.  

    ```bash
    [Unit]
    Description=Jupyter Notebook 

    [Service]
    Type=simple
    User=jetson
    ExecStart=/bin/sh -c "jupyter lab --ip=0.0.0.0 --no-browser --allow-root"
    WorkingDirectory=/home/jetson
    Restart=Always

    [Install]
    WantedBy=multi-user.target
    ```

    > Note: If you have a username other than "jetson" or want to launch Jupyter from a directory other than "/home/jetson", modify the file "User" and "WorkingDirectory" fields accordingly.

2. Copy the file to the directory ``/etc/systemd/system`` so it can be discovered as a system service.

    ```bash
    sudo cp jetbot_jupyter.service /etc/systemd/system/jetbot_jupyter.service
    ```

3. Enable the system service to run at boot

    ```bash
    sudo systemctl enable jetbot_jupyter
    ```

Now, when you re-boot your Jetson, the Jupyter lab server should start in the background.  

That's great, but in order to connect to the server, you need to know it's IP address.  The last step will be to enable a system service that displays the IP address on the JetBot's PiOLED display upon boot.

### Step 4 - Create system service to show the IP address upon boot

This is very similar to creating a service for the Jupyter Lab server, we're just changing the application that's launched

1. Create a file named ``jetbot_display.service`` and add the following content.

    ```bash
    [Unit]
    Description=Jupyter Notebook 

    [Service]
    Type=simple
    User=jetson
    ExecStart=/bin/sh -c "python3 -m jetbot.apps.stats"
    WorkingDirectory=/home/jetson
    Restart=Always

    [Install]
    WantedBy=multi-user.target
    ```

2. Copy the file to the directory ``/etc/systemd/system`` so it can be discovered as a system service.

    ```bash
    sudo cp jetbot_display.service /etc/systemd/system/jetbot_display.service
    ```

3. Enable the system service to run at boot

    ```bash
    sudo systemctl enable jetbot_display
    ```

That's it!  Now you should be able to reboot the JetBot, and it's IP address should automatically show up on the PiOLED display.

We hope this helps you create a custom native system configuration for using JetBot.  If you have any questions or see any issues with this guide, please [create an issue on GitHub](https://github.com/NVIDIA-AI-IOT/jetbot/issues).

Happy hacking!

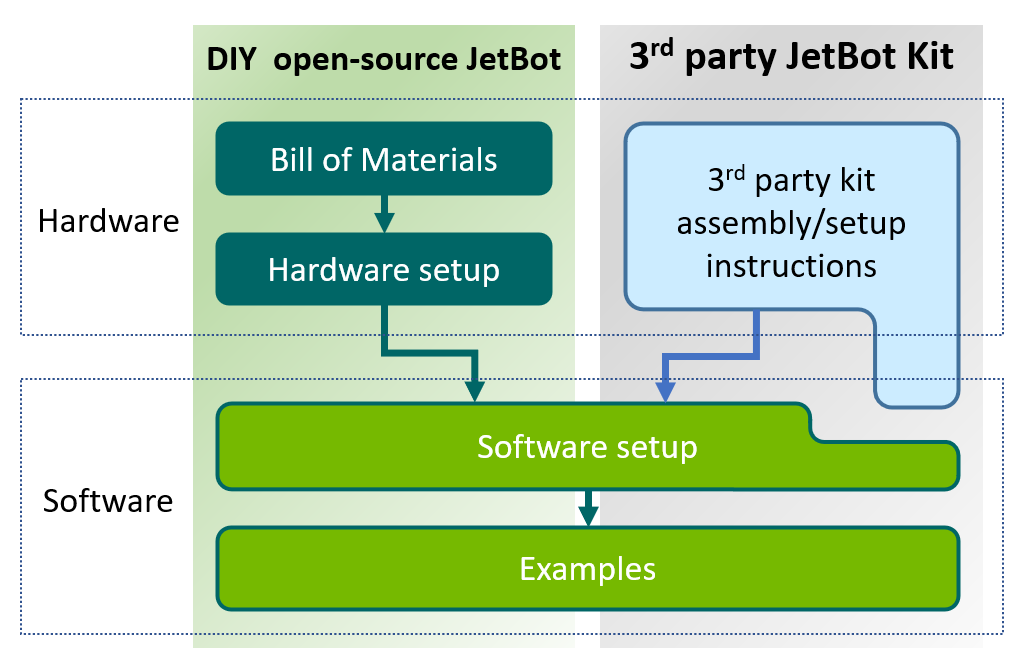
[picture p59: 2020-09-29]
docs/images/jetbot_getting_started_steps.png

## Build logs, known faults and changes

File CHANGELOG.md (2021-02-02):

# Changes

## [Master]

## [0.4.3]

### Added

- Added ``LocalController`` class which allows users to directly connect controller to JetBot

## [0.4.2] - 11/10/2020

### Fixed

- Resolved software issue which affected certain motor driver variants

## [0.4.1] - 10/22/2020

### Added

- ZMQ Camera publisher to improve stability of Camera and allow camera use in multiple notebooks
- Docker containers for ML dependencies, PiOLED display, ZMQ Camera publisher, and Jupyter Lab server
- Inline documentation using mkdocs-material and mike

### Changed

- Default ``Camera`` class now uses ZMQ Camera.  This means you must run the ZMQ camera publisher to access the camera as before.  If you wish to use the old Camera class, do ```from jetbot.camera.opencv_gst_camera import OpenCvGstCamera``` and ``camera = OpenCvGstCamera()``

### Deprecated

- JetPack 4.3 SD card image

### Fixed

- Camera shutdown failures are avoided by addition of ZMQ Camera. No longer need for constant ``systemctl restart nvargus-daemon`` calls.
- Camera queue buildup for heavier image processing workloads is fixed in ZMQ Camera by dropping old frames using conflate option.

## [0.4.0] - 1/15/2020

### Added

- Added support for JetPack 4.3 SD card image.  Found [here](https://drive.google.com/open?id=1G5nw0o3Q6E08xZM99ZfzQAe7-qAXxzHN).

### Changed

- Updated Object Detector SD card image.  Found [here](https://drive.google.com/open?id=1KjlDMRD8uhgQmQK-nC2CZGHFTbq4qQQH)

## [0.3.0] - 3/9/2019

### Added

- Initial release with JetPack 4.2 SD card image.  Found [here](https://drive.google.com/open?id=1RgQ99QOqhcNxivSNJpetXdoOCqUWAWH_)

[Master]: https://github.com/NVIDIA-AI-IOT/jetbot/compare/v0.4.0...HEAD
[0.4.0]: https://github.com/NVIDIA-AI-IOT/jetbot/compare/v0.3.0...v0.4.0
[0.3.0]: https://github.com/NVIDIA-AI-IOT/jetbot/releases/tag/v0.3.0

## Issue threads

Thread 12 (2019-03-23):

JetBot 零件清单中国区购买链接汇总

unbug, 2019-03-23:
This issue is meant to help Chinese devs to buy the materials of JetBot in China. I'll keep updating it, any help is welcome.

Its appreciate leaving the issue open for a while, thanks.

中国区购买 JetBot 的零件比较麻烦，所以整理了一个可以在国内购买的列表，欢迎一起更新汇总。

https://github.com/unbug/NVIDIA-JetBot-Diy/wiki

jaybdub, 2019-03-25:
Thanks unbug, we look forward to seeing how your fork progresses.

John

unbug, 2019-03-26:
Hey @jaybdub, the 3D printer is hard to find, do we have a cardboard option?

jaybdub, 2019-03-27:
Currently we just have the 3D printed chassis design.

You could possibly build an alternate chassis however you like.  To work well, the most important aspect is to place the camera in the correct orientation.

If you design an alternative chassis in your fork, let us know!  Potentially this could be useful to others.

John

unbug, 2019-03-27:
Hum...I believe we can just buy a toy car model, so we can focus on AI developing base on Jetson. I'll see what can I find.

unbug, 2019-03-27:
Hey @jaybdub, I found some cardboard, the size is matched Jetson nano. What do you think?

### Model 1, Smart Motor Robot Car Chassis Kit

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

[Taobao](https://item.taobao.com/item.htm?spm=a230r.1.14.160.4e3058d58fdH3n&id=562562707881&ns=1&abbucket=1#detail)

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

[Amazon](https://www.amazon.com/Emgreat%C2%AE-Chassis-Encoder-wheels-Battery/dp/B00GLO5SMY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)

### Model 2,
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

[Taobao](https://item.taobao.com/item.htm?id=578766841591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)

### Model 3,
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

[Taobao](https://item.taobao.com/item.htm?spm=a230r.1.14.87.127c6d0fbNWE5g&id=566000074468&ns=1&abbucket=1#detail)

### Model 4,
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

[Taobao](https://item.taobao.com/item.htm?spm=a230r.1.14.96.4e3058d58fdH3n&id=589010397546&ns=1&abbucket=1#detail)

unbug, 2019-04-03:
Hi @jaybdub do you have an answer to my proposal?

jaybdub, 2019-04-03:
Hi unbug,

Cool!  It looks like model 2 is the closest match and would likely be compatible with the other electronics in the bill of materials.

It seems the kit only includes the motors, wheels, caster and chassis.  So you would need to buy all of the other components.

You would also need to figure out how to mount the camera and Jetson Nano, as well as how to house the battery.

Best,
John

unbug, 2019-04-04:
Thanks, @jaybdub, model 1 works the same as model 2, so I think both of them are matched.

jaybdub, 2019-04-05:
They look pretty similar, just a few minor differences:

It looks like (2) uses the same motors in our bill of materials, so will work directly with the motor driver we list.

Also, we noticed that the cheap continuous rotation servos (like those used in (1)) tend to 'drift', and require frequent calibration.  Something to keep in mind!

Best,
John

unbug, 2019-04-05:
Thanks, @jaybdub.
Indeed, the drift is an issue.

mayuanjason, 2019-04-12:
Hi unbug,

You can try mbot, a metal car, please refer to the following webpage for more detailed info.
https://www.makeblock.com/steam-kits/mbot

unbug, 2019-04-13:
@mayuanjason Looks cool, have you tried it? Is it fit sie of Jetson? I'll investigate further, thanks.

mayuanjason, 2019-04-13:
Hi unbug,
No, but I think this plan can work.
mBot has a Arduino board on it, jetson nano can communicate with Arduino through serial port, so the control path is something like below:
Command from jetson nano -> serial port -> Arduino -> motor(e.g. start, stop)
And we can use pyserial library for serial communication from jetson side, and there also has some serial related functions in Arduino side.

unbug, 2019-05-05:
Good news @jaybdub , check out some showcase of Jetbot build by Chinese devs, some of them even success use a third party robot car model. https://github.com/open-ai-robot/NVIDIA-JetBot-Diy/issues/6

wujiang, 2019-06-19:
We created a kit for anyone to order online https://curious.voyage/

unbug, 2019-06-19:
@wujiang thanks. Do we have to pay the shipping fee and customs duties if we order to China?

wujiang, 2019-06-19:
@unbug np. Yes, you'll need to pay for the shipping. Not sure about tariff.

jasper-hue, 2019-10-05:
Hey @unbug ,

I tried your approach of using PCA9685 as the motor driver,
But can you explain to me how can we connect the dc motor in that.
PCA9685 is a servo driver and has 3 pins Gnd , V+ and PWM, the DC motor only has two.
Any idea how you are planning to connect them together ?

Thanks in advance.

unbug, 2019-10-05:
Here are some success cases https://github.com/open-ai-robot/awesome-nvidia-jetson/issues/6

Closed 2022-07-15.

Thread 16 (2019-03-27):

Size of power bank?

port513, 2019-03-27:
Since there is no way to ship to Sweden if it's LiPO, what size of power bank should I choose?

tokk-nv, 2019-03-29:
The battery bay of the chassis is following, so the battery needs to be smaller than this.

- Length: **136mm**
- Width: **71mm**
- Height: **20mm**

I hope you can find a compatible battery.
Then you can make a fork of this project to show the Swedish version of the BOM.

agrobler58, 2019-04-03:
Same issue here. Suggested INIU model is hard to obtain in Australia. Regarding power, do both ports need to have 3A? Or is it OK if one of them (for motors) has 2.4A?

aussetg, 2019-04-06:
I don't think the battery is capable to output 5v 3a on each ports at once, it's probably 3a in total. If they say it can it's probably a lie tbh.

einsteinagogo, 2019-04-18:
This could be make or break for Europe, trying to find a battery which fits. I've just ordered the following..

which supports 3A/5V on both USB ports, but it's maybe too wide..

https://www.amazon.co.uk/gp/product/B07KMRCM6Y/ref=ppx_yo_dt_b_asin_title_o01_s00?ie=UTF8&psc=1

We will see....

http://andysworld.org.uk/2019/04/18/can-you-guess-what-it-is-yet/

einsteinagogo, 2019-04-18:
where does the 3A/5v come from as the Description of that Power Bank states

Output: 2.4A Output for each 2 USB port

davinderc, 2019-05-17:
@einsteinagogo where you able to make it work? I ordered an Ansmann 10.8 QC 3.0, but then ran into a problem using the USB C output because of the QC 3.0 protocol.

einsteinagogo, 2019-05-17:
@davinderc I've been trying MANY different power banks available in the UK, I now have two which work, BUT they DO NOT FIT!!!

e.g. they correctly BOOT the NANO, rather than just booting and dying.

Does this Ansmann 10.8 QC 3.0 fit ?

I've now been discussing power banks for Import from China, which fit and deliver 3A/5V from both USB connectors.

I'm now ready to start building this weekend, after having a delay in obtaining original parts, and also printing the chassis which has been done.

davinderc, 2019-05-17:
@einsteinagogo The Ansmann 10.8 QC 3.0 fits, and is just slightly loose vertically. It boots the Nano just fine, although if I remember correctly, you need to push the button on the powerbank before plugging the nano in. But you will need to resolve the QC 3.0 issue. I borrowed this [adapter](https://www.digitec.ch/en/s1/product/dell-usb-c-to-usb-30-vga-hdmi-ethernet-lan-notebook-adapters-5668957) to be able to use the USB C output.

By the way, as far as I know, standard USB (non-C) connectors are not built for more than 2 or 2.1 A, and most powerbanks of this size don't provide more than 2.1-2.4 A combined from both ports, so I would be wary of any powerbanks that state they can provide 3A without using a USB C or other port. That much power output seems very uncommon for this size powerbank. I'm going to measure the power consumption of both the board and the driver on Monday, so I can find a more suitable powerbank (without QC 3.0).

einsteinagogo, 2019-05-17:
@davinderc I just going by the Power Bank which is stated from the Bill of Materials, it states 3A from both ports...

I've test current consumption at BOOT and it does not seem alot, but clearly I have many power banks, which do not work, they start the device, but later go off.

davinderc, 2019-05-17:
FYI, the one you linked is wider and thicker than the dimensions cited at the top of this page.

Yeah, it says that, but that's advertising. If you try it, good luck and let us know how it works. I personally wouldn't buy it without knowing for sure and that's why Monday I intend to measure current first. Also, the current consumption will go up when you use the GPU for CNNs on images.

einsteinagogo, 2019-05-17:
yes I stated that "but it's maybe too wide.".

but it works fully, and I've got two different units which are working, they'll just fit in the battery compartment!

The other's are arriving direct from China, and are test samples, if they work I'll report here.

davinderc, 2019-05-21:
So I've found around 1.5 A peak power draw by the Nano while running obstacle avoidance (note I am running it at the half-power setting) and 1.5 A locked motor current draw if I set the motors to 0.9 and 0.75. You can run the whole thing on 2 A if you don't set the motors too high.

einsteinagogo, 2019-05-21:
Now I have my Jetbot built, I'm experimenting with a power bank which fits, and having no issues currently going through the examples, at half-power-setting-5watts.

(this power bank booted before and went off before, but silly me did have ethernet, usb mouse, usb keyboard and HDMI connected! - I suspect ethernet port is the issue!)

other than I think one of my TT motors is duff, because the balance is wrong, e.g. at 0.3 right motor does not drive....so new motors on the way to experiment more.

davinderc, 2019-05-22:
The motors are usually not the same, so I found that I had to simply set their velocities proportionally different. Even if you get new motors, you might find those are not the same also. For me 0.3 was the minimum to drive the motors, but a little more was better.

Also, I bought an external power supply for the Jetson so that I could run it without the powerbank if I wanted to. We used that to power it up and configure it to connect to the Wifi first, then afterwards just booted and waited for Wifi connect and commanded it through the Jupyter notebook. We had no issues with lack of power after that.

einsteinagogo, 2019-05-22:
@davinderc thanks for that tip about motors! that explains that!

Looks like I'll have to find the sweet spot for forward!!! then otherwise I'll go round in circles!

I already have power supplies which I use... but not good tethered...

davinderc, 2019-05-22:
Oh yes, the power supplies are just useful for initial configs or when you don't intend to run the motors. It's horrible to run the motors with it tethered.

As for the motors, once you find a proportion that keeps the motors moving straight (took me 2-3 tries using the set_motors method), you can probably set those as constants somewhere in your code. I couldn't figure out how to do it when I was looking at it, but I did see that the source code has a way to do it so that you can simply call the forward method and forget about the underlying motor differences.

einsteinagogo, 2019-05-25:
The battery in the BOM is NOW available in the UK via Amazon after discussions with Topstar (INIU)

https://amzn.to/2VRAwWC

davinderc, 2019-05-25:
CC: @tokk-nv looks like we've got advertising using Amazon affiliate links...

ergoen, 2019-06-06:
> Since there is no way to ship to Sweden if it's LiPO, what size of power bank should I choose?

Sorry for writing in this old(-ish) topic, but where did you manage to order the correctly sized plastic ball in Sweden? I have been to various stores that I would imagine has items like this but have been met with odd stares.. :P

davinderc, 2019-06-06:
> Sorry for writing in this old(-ish) topic, but where did you manage to order the correctly sized plastic ball in Sweden? I have been to various stores that I would imagine has items like this but have been met with odd stares.. :P

So I found it easiest by searching for Pololu products. I took a look around and couldn't browse the Swedish shops all that easily (maybe because I'm in Germany or maybe because I don't understand Swedish). Not sure if this helps, but there's a shop in Finland that seems to have it: http://robomaa.fi/robotics/pololu-pallolaakeri-25cm-muovi
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
davinderc, 2019-06-06:
According to this Google image search on the site, they have it, but I can't seem to open their site, no idea why... Are you guys suffering from internet issues? (a traceroute seems to get to Swedish domains, and then times out)

https://www.google.com/search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

davinderc, 2019-06-06:
EDIT: got it, here it is: https://www.lawicel-shop.se/pololu-ball-caster-with-25mm-plastic-ball
@ergoen

ergoen, 2019-06-06:
Wow thanks @davinderc ! It seems I was searching for the wrong term :)

davinderc, 2019-06-06:
It's kind of funny, I was searching for the wrong term here in Germany as well and then I asked a co-worker and a couple of searches and minutes later he had found exactly what I needed! By the way, I just used the ball and printed the caster they provided, works great!

ergoen, 2019-06-06:
Good to know! I have ordered one as well now! Thanks again

ChristophWenk, 2019-10-23:
The power bank used in the BOM is not available here in Switzerland.

So I have tried the goobay Quick Charge Qualcomm (10000mAh) but it just booted the Nano for like 30 seconds and then it shut down again. Sometimes it was able to boot the Nano but it shutdown immediately when I tried to use the motors.
It only worked when I powered just the Nano with it and the motors separately with my computer. But that cannot be a solution.

Which alternative power bank that fits is able to support the power draw from all the components?

davinderc13, 2019-10-23:
@ChristophWenk I believe I mentioned one option that worked for me up above.

ergoen, 2019-10-23:
I bought a "GP Powerbank Voyage 2 / 10000 mAh", this works and fits also

ChristophWenk, 2019-10-23:
@ergoen Thanks for the suggestion. The specifications mention that it has 2 x USB-A DC 5V/2.4A. Does that mean the 3A for each port mentioned above are not needed after all?

ergoen, 2019-10-23:
I suspect it's the total combined power that has to support 3A, not per port. So any Powerbank that has a 3A usb-c port should in theory be fine (?). The goobay one you linked should therefore also work.. The specs seem identical to the GP one I have.

ChristophWenk, 2019-10-23:
Aha. But then you also used a USB-C cable instead of the USB-A mentioned in the BOM? Sorry for all the questions, I am not particularly familiar with this kind of stuff.

ergoen, 2019-10-23:
I'm only using the two USB-A ports, not the C. I didn't really do any research before buying it, just that it could output 3A :p

ChristophWenk, 2019-10-23:
Ok. The same as I did then. I just ordered a unit of the model you mentioned and will try get it to work with that one.
I will post an update if I was successful.

davinderc13, 2019-10-23:
@ergoen @ChristophWenk it would be wonderful if you guys could chat somewhere else about this, as I don't enjoy receiving notifications about the same discussion I had long ago (and is clearly described up above, although Christoph doesn't feel like reading it). I've tried unsubscribing from this thread and I'm still receiving emails with your discussions. Please, could you discuss it elsewhere?

davinderc13, 2019-10-23:
@tokk-nv could this issue be closed, since it has already been thoroughly discussed and resolved?

ChristophWenk, 2019-10-23:
@davinderc13 Just to be clear: I read through the whole issue. All I found was workaround solutions. I'd like to have a clean solution that works out of the box like the one mentioned in the BOM.
Also, there is an notifications "Unsubscribe" Button on the top right.

davinderc13, 2019-10-23:
@ChristophWenk then you've misunderstood what I wrote or intentionally ignored it. I had the exact same questions that you did and discussed/resolved them.

As for clicking the unsubscribe button, that's a "workaround" as you put it, because I did click it and find that I am once again subscribed to it. Please open another issue rather than dig up an old one and pester other people.

davinderc13, 2019-10-23:
@tokk-nv as I mentioned before, the unsubscribe button does not seem to have any effect and the original OP has not followed up on this thread, nor does it seem there will ever be a resolution that will satisfy everyone around the world. Could you please close it so I can stop receiving emails about it?

Closed 2022-07-15.

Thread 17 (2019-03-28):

Is the 3D model open source?

TickPi, 2019-03-28:
A 60 mm diameter TT motor tire was not found on the Chinese e-commerce website. This is not a common commodity. The 65mm diameter TT motor tires are very numerous and have been widely used in various intelligent robot cars. So I want to modify the 3D model to fit the 65mm wheel.
thanks.

wahid, 2019-03-29:
Wouldn't the 65mm tire work without motification?

sirwalterrrich, 2019-03-29:
@Wujupi You can convert the .stl file to a solid using software like fusion360 and then modify it to your liking.  How to video link below.

https://youtu.be/yO6hboYWnfM

tokk-nv, 2019-03-30:
Hi wujupi, and all,
We also realized 65mm wheels are more widely available, so we are trying to accommodate that.
If we just swap the 60mm wheels with 65mm wheels, it would tilt the robot chassis and change the camera orientation, so we'd want to also raise the caster part by 2.5mm.

For now, I designed the caster parts designed for 65mm wheels and put them (along with STEP and IGEL files) under a branch.
I'm making a pull request, so for now please check the branch.
https://github.com/NVIDIA-AI-IOT/jetbot/pull/20

wujupi, 2019-04-03:
@sirwalterrrich @tokk-nv Thank you, Thank you, I have printed the 65mm model and installed it on the jetbot, it works perfectly.

storagejarett, 2019-04-03:
The body is really poorly designed for modularity.  If a change to wheels needs 100% remodeling and reprint, it won't work for most people.

This should be a modular design, where they let item is at a fixed location/height and the rest of the components can be modified individually.

There is way too much design around Adafruit/Amazon specific parts which are not guaranteed availability in all countries.

Also, the existing design, no matter what the orientation, has massive amount of overhanging elements which can be difficult to print without massive amount of supports.

Key points:. Height and position of camera.

In my build, I am:
* using 2 smaller individual motor drivers instead of the long double driver
* Using either 18650 batteries or a 4s lipo pack + buck power converter to bring 12-14v down to 5v
* Using a different camera
* Possibly using tracks instead of wheels + caster

There should be camera location mount with optional camera mounts.  A base body it connects to. And the rest of the components have modular attachment.

The Nano board on top may not be the best way to go about this either. If it was bottom mounted or in the chassis, all the other parts could build around and on top of it.

Agent-Cain, 2019-04-23:
What is supposed to be mounted in the lower front ?

Closed 2022-07-15.

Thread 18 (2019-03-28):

GPIO & Adafruit MotorHat

maximecb, 2019-03-28:
Hi. I see that the Jetbot is using the Adafruit MotorHat library, which was originally designed for the Raspberri Pi. I'm currently [running into issues](https://devtalk.nvidia.com/default/topic/1049116/jetson-nano/python-gpio-support-/) trying to get the RPi.GPIO library to work. I was wondering if you had any pointers on how to get the Python RPi GPIO libs to work on the Jetson Nano? Are there packages to install, etc?

jaybdub, 2019-03-28:
Hi maximecb,

The Jetson.GPIO library (which is actually also importable as RPi.GPIO) is already pre-installed if you're using Jetson Nano or the latest JetPack.  It's located at  ``/opt/nvidia/jetson-gpio``.

Make sure that you uninstall other versions of RPi.GPIO that you may have installed.

Then, there's a bit of extra setup that needs to be done to use the Jetson.GPIO library

#### Step 1 - Setup permissions

Execute the following from a terminal on your Jetson

```bash
sudo groupadd -f -r gpio
sudo usermod -a -G gpio $USER
sudo cp /opt/nvidia/jetson-gpio/etc/99-gpio.rules /etc/udev/rules.d/
sudo udevadm control --reload-rules && sudo udevadm trigger
```

Then, reboot the Jetson

```bash
sudo reboot now
```

#### Step 2 - Extend python path

Add the following in your python script before calls to import the RPi.GPIO library (or libraries that use it like the motorhat library)

```python
import sys
sys.path.append('/opt/nvidia/jetson-gpio/lib/python/')
sys.path.append('/opt/nvidia/jetson-gpio/lib/python/Jetson/GPIO')
```

You should then be able to import the Jetson.GPIO

```python
import Jetson.GPIO
```

or equivalently,

```python
import RPi.GPIO
```

I haven't tested this with the MotorHat library yet, but I was able to import RPi.GPIO after these steps.

Let me know if you run into issues, or if these steps work for you.  I think this will be valuable to others.

Best,
John

maximecb, 2019-03-28:
Thanks for taking the time to write these instructions John. I am able to import the lib and make an LED flash. I will look again at Pypot (I2C) and the motor shield in the next couple of days.

maximecb, 2019-03-28:
I2C seems to work as well. Thanks again John!

jaybdub, 2019-03-28:
Awesome!  Thanks for verifying, this will be helpful for others.

Let me know if you run into other issues.

John

maximecb, 2019-03-29:
Small update: I've been made aware that the Jetson.GPIO package is now available through pip:
https://pypi.org/project/Jetson.GPIO/

Also, there doesn't seem to be PWM support available on the GPIO package that comes with the Jetson OS image. For my application (driving a DC motor), software PWM is probably doable, but hardware PWM would be even better.

jaybdub, 2019-03-29:
You're correct.  Jetson.GPIO doesn't support PWM.  However, the following I2C controlled board can generate PWM signals up to ~1.6kHz and should have Python libraries available.

https://www.adafruit.com/product/815

You could potentially connect this to whatever H-Bridge meets the power requirements of your application.  The motor driver we used for JetBot actually combines this chip and multiple H-bridge on the same board.

https://www.adafruit.com/product/2927

Depending on what your application, that may just work!

John

weiqing-beijing, 2019-04-06:
Hi @jaybdub , thanks for the guide. Very helpful!

One more question regarding the spi and i2s. The document mentioned there are spi and i2s pins. Do you know how to activate and use those pins? Or if there are any documentation as reference.

Thanks, wq

Closed 2022-07-15.

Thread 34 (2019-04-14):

What is the maximum power draw of the Nano ?

aussetg, 2019-04-14:
Is 15w enough ? Or should you prepare for 20w ?

tokk-nv, 2019-04-18:
Hello aussetg,
The total system power consumption depends on many factors including devices attached to the USB 3.0 Type-A ports.
If you are seeing a potential power issue, I think it is worth considering supplying power through the DC barrel jack (which is rated for 5V/4A, thus 20W).

RyanC1681, 2019-05-12:
Hi,
   I tried both nano and JetBot image with a 5V/2.1A power bank, but the power bank couldn't boot up the system. My power bank has a 2.1 A and 1A port, so can I use both ports at the same time to supply 3.1A power to the Nano? I tried to short J48 with both DC plug and uUSB came from power bank, but it did not work.  Could you recommend a way to supply more current using a power bank? Thanks.

davinderc, 2019-05-17:
@RyanC1681 Is your powerbank really able to provide 3.1 A total? Most powerbanks I've found that fit the provided chassis have two outputs but a maximum combined output of 2.1-2.4 A. I found a powerbank that has a USB C output with Quick Charge 3.0 can provide more, but then I ran into the problem of the QC 3.0 protocol needing to be implemented by whatever device is connected to that.

davinderc, 2019-05-21:
@RyanC1681 I've found that the Nano requires from 0.5-1.5 A of current. During boot up it doesn't seem to go over 1 A, and around 1.5 is peak during object detection, but maybe it peaks a bit higher and my USB power meter wasn't fast enough to spot it. The driver depends on how fast you run the motors, when I set one to 0.9 and the other to 0.75, I was getting around 1.5 A locked motor current, but around 0.5 A free spinning. So ideally we should have 3 A total available, but it's not a constant current requirement.

einsteinagogo, 2019-05-25:
The battery in the BOM is NOW available in the UK via Amazon after discussions with Topstar (INIU)

https://amzn.to/2VRAwWC

davinderc, 2019-05-25:
> The battery in the BOM is NOW available in the UK via Amazon after discussions with Topstar (INIU)
>
> https://amzn.to/2VRAwWC

Is that an affiliate link I see there?

davinderc, 2019-05-25:
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

@einsteinagogo
Is that an affiliate link I see there?

Closed 2022-07-15.

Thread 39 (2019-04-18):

Comments on Setup Instructions

wphuhn, 2019-04-18:
After waiting weeks for all the parts to arrive, learning to 3D print, and (re-)learning how to solder, I managed to build my Jetbot and it didn't catch on fire (see https://twitter.com/william_p_huhn/status/1118720548157128705).  I have a few suggestions for changes to the instructions, which I've grouped by section.  Hope these help.

## Hardware Setup ##

* "Tools Needed"
   * Some form of precision jeweler/electronics screwdriver set should be added.  Securing the power and motor wires to the motor driver without them took a considerable amount of effort.
* "Step 2 - Mount motors"
   * It should be mentioned that the motors are attached with the M3 screws *and nuts*.
* "Step 4 - Strip motor driver power cable"
   * It's mentioned to remove the green and white wires, but the final diagram shows them twisted and not removed.
* "Step 10 - Solder header onto PiOLED display"
   * A schematic diagram for which connections should be soldered and which wires go where would be hugely useful for this step and the next.  The camera angle makes it difficult to see.
* "Step 11 - Wire motor driver to PiOLED display"
   * The color contrast between orange and yellow is really bad in the picture.  I had to go look at pictures in subsequent steps to figure out which was which.
   * The instructions reference SDA (orange) and SCL (yellow), which I realize are the proper names, but they're labeled 3 and 5 on the board itself.
* "Step 13 - Attach wide angle sensor"
   * This step should come before "Step 12 - Mount camera", as it's much easier to attach the wide angle sensor without having to account for the angle of the mount on the Jetbot.
   * This is obvious, but the instructions never state to take the camera lens off.
* "Step 15 - Organize wires"
   * The pictures in this section shows the Jetbot's power wires hooked up so that the motor will draw power, which I imagine most people will do even though it's not explicitly stated to do so, but Step 2 of the Software Setup specifically states that we should not power the motor until after the first booting/initial setup.  I think a notice to not power the Jetbot yet would be useful.
* Miscellaneous
   * This is really obvious, but the instructions never state to attach the wheels.  (It looks like it happens sometime between Step 9 and 11.)

## Software Setup ##

* "Step 5 - Install latest software (optional)"
   * On an JetBot SD image that I flashed yesterday night (18 April, 2019), `rsync` was not installed by default, but it was easily installable via `apt`.
   * The user will need to change directory up one level before running `rsync jetbot/notebooks ~/Notebooks`.

## Examples ##

* "Example 2 - Teleoperation"
   * The widget for controlling the Jetbot via my Xbox One controller never showed up, although <https://html5gamepad.com/> was able to detect it.  No error messages or anything.

arraypan, 2019-04-18:
How did you get the wheels, they are still out of stocks

wphuhn, 2019-04-18:
@arraypan I used the 65mm wheels and the associated caster STLs, as they've been in stock for a while (and still appear to be, according to the Adafruit website.)

arraypan, 2019-04-19:
Thanks, I just saw this.

jaybdub, 2019-04-20:
Hi wphuhn,

Thanks for this very thorough feedback!

I think you make a lot of good points.  I'll leave this issue open until we can scope and address these.

Glad to hear you finished building!  Hope you're having fun, if you find any other issues please let us know.

Thanks!
John

coppoljja, 2019-05-07:
Motor controller power cable is the other one than depicted.

Closed 2022-07-15.

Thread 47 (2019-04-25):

Camera (streaming) does not work

dvillevald, 2019-04-25:
I am trying to run a data_collection notebook and have an issue with the camera - the cell which creates a camera instance takes forever to run and, when/if it is executed, the streaming only works for few seconds (if work at all) and then the image becomes still and does not change. Do you have any suggestions on how to resolve it? Thank you in advance.

jaybdub, 2019-04-25:
Hi dvillevald,

Thanks for reaching out!  We have encountered camera freezing with the object detection notebook which were are looking into, but have not been able to reproduce for the data_collection notebook.

Could you try restarting the notebook and executing the following from a terminal before initializing the Camera?

```bash
sudo systemctl restart nvargus-daemon
```

Also, could you provide the following information (which will be helpful in tracking this problem down).

1.  Are you using the listed battery pack?  If so, roughly what is the battery %.
2.  Do you have any other open jupyter notebooks?  The camera can only be initialized in a single one at a time.
3.  Is the Jetson Nano in MAXN or 5W mode?  You can determine this by calling the following from a terminal

    ```bash
    nvpmodel -q
    ```

Thank you!
John

dvillevald, 2019-04-26:
Hi John,

Thanks a lot for looking into this!

Yes, I tried `sudo systemctl restart nvargus-daemon`  before initializing the camera but it does not seem to help.

_1. Are you using the listed battery pack? If so, roughly what is the battery %._
Yes, I use the pack mentioned in the bills of materials (100% charged). I also observed the same behavior with (stationary) power supply.

_2. Do you have any other open jupyter notebooks? The camera can only be initialized in a single one at a time._
I only run one notebook data_collection - I see only one kernel running.

_3. Is the Jetson Nano in MAXN or 5W mode?_
I got the following when I run `nvpmodel -q`  and it shows 5W.
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

In case it might help -

- I have the issue described above when I use Chrome.  When I try to connect from Internet Explorer and run the same data_collection notebook, I cannot initialize the camera - after trying to run the cell initializing the camera I get **Error creating widget: could not find the model**
- I am on Windows 10 (with NVIDIA GeForce GTX 1050 Ti.)

Thank you again for helping!
Dmitri

jaybdub, 2019-04-26:
Hi Dmitri,

Thanks for sharing, this is helpful.  The error in screenshot you shared indicates the failure occurs when initializing the camera on the robot.  If that's the case, the error may be contained in the camera daemon log or the jupyter kernel log.  Can you call the following

```bash
journalctl -u jetbot_jupyter >> jupyter_log.txt
journalctl -u nvargus-daemon >> nvargus_log.txt
```

This will dump the logs into two files ``jupyter_log.txt`` and ``nvargus_log.txt``.  You can then download these files to your computer.  Could you share these logs with me?

Thank you!
John

dvillevald, 2019-04-27:
Hi John,

Thank you for following up! I am attaching the logs. Please let me know if you want me to run more tests.
[nvargus_log.txt](https://github.com/NVIDIA-AI-IOT/jetbot/files/3123322/nvargus_log.txt)
[jupyter_log.txt](https://github.com/NVIDIA-AI-IOT/jetbot/files/3123323/jupyter_log.txt)

Thank you.
Dmitri

dvillevald, 2019-05-03:
Any suggestions?

dvillevald, 2019-05-04:
I replaced the camera and it works ok so it seems something was wrong with the camera (or the connection cable.)

Thank you for looking into this!

Closed 2019-05-04.

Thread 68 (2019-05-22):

Left deviation

ddwy, 2019-05-22:
Why does my jetbot go left when going straight and backward?

aileenZhang, 2019-05-22:
Maybe you should check your power bank

jaybdub, 2019-05-23:
Hi ddwy,

Usually, due to slippage, friction and other factors throughout the system, the robot will either tend slightly to the right or left.  If the drift is extreme, could you check to see if there is anything adding resistance to one of the wheels?

Is the robot spinning in place?  If so, one of the motors may be wired backwards.

John

ddwy, 2019-05-23:
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

Hello, my situation is like this. When the car moves forward, it will move slowly to the left.

wjzhou, 2019-05-23:
I think this is unavoidable in the current open-loop control setup.
Even with the same pwm, the motors will spin slightly differently,  the car will turn slowly.

You may hold the cart, and check both motor spins as expected

ddwy, 2019-05-24:
The problem has not been solved yet.

einsteinagogo, 2019-05-25:
or because motors have different deviations!

The TT Motor described here on the PiHiut states

https://thepihut.com/products/adafruit-dc-gearbox-motor-tt-motor-200rpm-3-to-6vdc-ada3777

Note that these are very basic motors, and have no built-in encoders, speed control or positional feedback. Voltage goes in, rotation goes out! T**here will be variation from motor to motor**, so a separate feedback system is required if you need precision movement.

mine is also the same.

jaybdub, 2019-05-26:
Yep!

Drift is unavoidable with this open-loop control scheme.  By calibrating, you can reduce the rate that the robot drifts.

Actually, the motor implementation has an ``alpha`` and ``beta`` value which may be used to linearly calibrate each motor.  The command, ``y`` sent to the motor is calculated from the input value ``x`` as

``y = alpha * x + beta``

You could adjust these parameters to linearly calibrate each motor with software.  For example,

```python
robot.left_motor.alpha = 0.3
robot.right_motor.alpha = 0.7
```

Attaching them to sliders will probably make live calibration a lot easier.  The results wont be perfect, but might help a bit.

Please let me know if you have any questions.

Best,
John

einsteinagogo, 2019-05-29:
I also found that using a better battery, for motors and Jetson Nano, deviation was less! and the robot could be controlled and go forward with less calibration.

Still needs a little tweaking, but worth checking if you battery can supply what is required.

LuisM78, 2019-11-04:
I am having the same proble. Do you know of a better robot platform for the jetson nano?
Thanks,
Luis

Closed 2022-07-15.

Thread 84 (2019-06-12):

the first example run is error

zouzhe1, 2019-06-12:
basic motion
from jetbot import Robot  ------->ok
robot =Robot()--------------error

---------------------------------------------------------------------------
OSError                                   Traceback (most recent call last)
<ipython-input-2-b418ad9f6ab3> in <module>
----> 1 robot = Robot()

/usr/local/lib/python3.6/dist-packages/jetbot-0.3.0-py3.6.egg/jetbot/robot.py in __init__(self, *args, **kwargs)
     20     def __init__(self, *args, **kwargs):
     21         super(Robot, self).__init__(*args, **kwargs)
---> 22         self.motor_driver = Adafruit_MotorHAT(i2c_bus=self.i2c_bus)
     23         self.left_motor = Motor(self.motor_driver, channel=self.left_motor_channel, alpha=self.left_motor_alpha)
     24         self.right_motor = Motor(self.motor_driver, channel=self.right_motor_channel, alpha=self.right_motor_alpha)

/usr/local/lib/python3.6/dist-packages/Adafruit_MotorHAT-1.4.0-py3.6.egg/Adafruit_MotorHAT/Adafruit_MotorHAT_Motors.py in __init__(self, addr, freq, i2c, i2c_bus)
    229         self.motors = [ Adafruit_DCMotor(self, m) for m in range(4) ]
    230         self.steppers = [ Adafruit_StepperMotor(self, 1), Adafruit_StepperMotor(self, 2) ]
--> 231         self._pwm = PWM(addr, debug=False, i2c=i2c, i2c_bus=i2c_bus)
    232         self._pwm.setPWMFreq(self._frequency)
    233

/usr/local/lib/python3.6/dist-packages/Adafruit_MotorHAT-1.4.0-py3.6.egg/Adafruit_MotorHAT/Adafruit_PWM_Servo_Driver.py in __init__(self, address, debug, i2c, i2c_bus)
     57         self.i2c = get_i2c_device(address, i2c, i2c_bus)
     58         logger.debug("Reseting PCA9685 MODE1 (without SLEEP) and MODE2")
---> 59         self.setAllPWM(0, 0)
     60         self.i2c.write8(self.__MODE2, self.__OUTDRV)
     61         self.i2c.write8(self.__MODE1, self.__ALLCALL)

/usr/local/lib/python3.6/dist-packages/Adafruit_MotorHAT-1.4.0-py3.6.egg/Adafruit_MotorHAT/Adafruit_PWM_Servo_Driver.py in setAllPWM(self, on, off)
     93     def setAllPWM(self, on, off):
     94         "Sets a all PWM channels"
---> 95         self.i2c.write8(self.__ALL_LED_ON_L, on & 0xFF)
     96         self.i2c.write8(self.__ALL_LED_ON_H, on >> 8)
     97         self.i2c.write8(self.__ALL_LED_OFF_L, off & 0xFF)

/usr/local/lib/python3.6/dist-packages/Adafruit_GPIO-1.0.3-py3.6.egg/Adafruit_GPIO/I2C.py in write8(self, register, value)
    114         """Write an 8-bit value to the specified register."""
    115         value = value & 0xFF
--> 116         self._bus.write_byte_data(self._address, register, value)
    117         self._logger.debug("Wrote 0x%02X to register 0x%02X",
    118                      value, register)

/usr/local/lib/python3.6/dist-packages/Adafruit_PureIO-0.2.3-py3.6.egg/Adafruit_PureIO/smbus.py in write_byte_data(self, addr, cmd, val)
    254         # Send the data to the device.
    255         self._select_device(addr)
--> 256         self._device.write(data)
    257
    258     def write_word_data(self, addr, cmd, val):

OSError: [Errno 121] Remote I/O error

Mubeeni35, 2019-06-12:
I got this error initially but it was fixed by reconnecting the wires.
Check to see if your motor driver is connected properly to the motors.
Try to plug in motor driver directly to the jetson nano pins without the PiOLED.

zouzhe1, 2019-06-12:
oh，its mean  the I2C  no  receive  ack  siginal？
i guessed this problem，so i connect to motor driven board，but still error，the address of I2C  jump pin  need  solder？

jaybdub, 2019-06-12:
Hi Zouzhe1,

We've noticed few common wiring errors that might cause this:

1.  The SDA / SCL wires are reversed.
2.  The 3.3V / GND wires are connected incorrectly.  Commonly it is thought that the 3.3V pin is at the corner of the motor driver board, but it's 1 pin offset from the corner.
3.  Weak solder connection

Could you double check to make sure these aren't the issue?

Thanks,
John

zouzhe1, 2019-06-14:
i very surely  the wires  is connected OK。
i use the module of motor driver from adafruit。
[https://www.adafruit.com/product/815](url)
because i see the chip   both are  PCA9685。
i2c address  is  default？

zouzhe1, 2019-06-14:
it is ok!i fonund my driver module A5 no connect VCC.
thank you again

Closed 2019-06-15.

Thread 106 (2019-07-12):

PiOLED display out of stock - alternatives?

vnguyen13, 2019-07-12:
Hi there,

The PiOLED display appears to be out of stock everywhere. Is there an alternative that could possibly work with this?

DouglasPearless, 2019-07-12:
If you are prepared to wait a week, I have been working with another and have completely redesigned the chassis so it takes a much bigger battery and a cheaper OLED display and a USB-C PD board to power it all...

It will be published on GitHub as a fork off the original repo.

Cheers
Douglas

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

vnguyen13, 2019-07-12:
That’s awesome! By any chance, is it going to be using the same Jetbot image? Because I’ve printed nearly 15 of the bodies so far for running a class... only to see that the pioled header is out of stock.

DouglasPearless, 2019-07-13:
I also have a design that allows a cheaper OLED to be mounted on a bracket that screws in using the existing mounting holes if you want that uploaded to?

Sent from my iPhone

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

vnguyen13, 2019-07-13:
Interesting! I’m curious to see what that looks like, sure!

--
Vu Nguyen
Carnegie Mellon Robotics Academy
cmu.edu/roboticsacademy<http://cmu.edu/roboticsacademy> | cs2n.org<http://cs2n.org>
Office: (412) 681-7160

On Jul 13, 2019, at 4:28 AM, Douglas Pearless <notifications@github.com<mailto:notifications@github.com>> wrote:

I also have a design that allows a cheaper OLED to be mounted on a bracket that screws in using the existing mounting holes if you want that uploaded to?

Sent from my iPhone

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

—
You are receiving this because you authored the thread.
Reply to this email directly, view it on GitHub<https://github.com/NVIDIA-AI-IOT/jetbot/issues/106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>, or mute the thread<https://github.com/notifications/unsubscribe-auth/AAI4OTYFOF6QHKI54KTQLETP7GG4TANCNFSM4ICSX3BA>.

DouglasPearless, 2019-07-14:
Have a look here https://github.com/DouglasPearless/jetbot for my updates …

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

vnguyen13, 2019-07-15:
Thanks Douglas! Is the image for the jetbot the same? As in, can we hotswap the new LCD screen with the one you have?

--
Vu Nguyen
Carnegie Mellon Robotics Academy
cmu.edu/roboticsacademy | cs2n.org
Office: (412) 681-7160

From: Douglas Pearless <notifications@github.com>
Reply-To: NVIDIA-AI-IOT/jetbot <reply@reply.github.com>
Date: Sunday, July 14, 2019 at 6:50 AM
To: NVIDIA-AI-IOT/jetbot <jetbot@noreply.github.com>
Cc: Vu Nguyen <vnguyen@nrec.ri.cmu.edu>, Author <author@noreply.github.com>
Subject: Re: [NVIDIA-AI-IOT/jetbot] PiOLED display out of stock - alternatives? (#106)

Have a look here https://github.com/DouglasPearless/jetbot for my updates …

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

—
You are receiving this because you authored the thread.
Reply to this email directly, view it on GitHub<https://github.com/NVIDIA-AI-IOT/jetbot/issues/106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>, or mute the thread<https://github.com/notifications/unsubscribe-auth/AAI4OT7I3VZMSLB34NPJIULP7MAGLANCNFSM4ICSX3BA>.

AustinPavlas, 2019-07-16:
Would it be possible to use this display instead of the PiOLED one? https://www.adafruit.com/product/931

It uses the same driver and I have been able to manually make it work but it does not work on boot.

vnguyen13, 2019-07-16:
@AustinPavlas That's awesome you got that one working! How did you get it to work manually?

AustinPavlas, 2019-07-16:
By running this file I am able to get the screen to run properly.

https://github.com/NVIDIA-AI-IOT/jetbot/blob/master/jetbot/apps/stats.py
This should be the same script that is initiated on boot but for some reason it only works when I manually run it.

vnguyen13, 2019-07-16:
Interesting!

@jaybdub any thoughts on @AustinPavlas's issue on it not running the script on boot for that screen?

vnguyen13, 2019-07-16:
@AustinPavlas while we're at it.. can you share how it's wired up?

AustinPavlas, 2019-07-16:
Current wiring is as follows:  SDA -> Pin 3 (SDA), SCL -> Pin 5 (SCL), GND -> Pin 6 (GND), and VIN -> Pin 1 (3V3).

Currently on boot the screen either remains completely blank or fills with random pixels.
I can fix this by connecting the RST pin to GND on the Nano then running the provided stats.py scripts which produces the expected output.  I have tried running the create_stats_service.py scripts which should configure the stats.py to run a service upon boot.  I have also tried to running the command via crontab to automatically run shortly after boot, but this does not seem to work either.

jaybdub, 2019-07-16:
Odd that stats.py would run when executed standalone, but not at boot.

Can you check to make sure the system service is enabled?

```bash
sudo systemctl enable jetbot_stats
sudo systemctl start jetbot_stats
```

Also, can you dump the log into a file by calling

```bash
journalctl -u jetbot_stats >> jetbot_stats.log
```

And upload this log?  This may have some indication of what's wrong.

Best,
John

AustinPavlas, 2019-07-17:
I have double checked that the system service is enabled.
[jetbot_stats.log](https://github.com/NVIDIA-AI-IOT/jetbot/files/3399545/jetbot_stats.log)
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
This is what shows on the screen after most boots, but connecting the RST pin to ground and rebooting the board fixes it most of the time.

Strangely enough, the final log about that did not show any error is was when the screen display what is shown above.

jaybdub, 2019-07-18:
Hmm,

The remote I/O error in the log is an indication that the service cannot connect with the display over I2C.

Is this possibly a hardware issue?  I notice the screen your using is a bit different.  Could you share the model as well as how you connected it to the JetBot?

Best,
John

vnguyen13, 2019-07-18:
Hi @jaybdub , @AustinPavlas mentioned that he used the following:
https://www.adafruit.com/product/931

And he gave the following information about how he connected it:

> Current wiring is as follows: SDA -> Pin 3 (SDA), SCL -> Pin 5 (SCL), GND -> Pin 6 (GND), and VIN -> Pin 1 (3V3).

DouglasPearless, 2019-07-21:
The LCD and OLED bracket uses the current chassis, it is designed to use the existing screw holes :-)

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

DouglasPearless, 2019-07-21:
I would expect you can hot swap the new LCD, note the OLED does not display until the JetBot has started up, it can take 1-2 mins.

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

vnguyen13, 2019-07-21:
Great! On your github page it doesn’t mention any specific screen. Do you have links to which one I should get?

DouglasPearless, 2019-07-22:
Ah,

I used this generic one:

https://hobbyelectronics.co.nz/product?SKU=377&Name=Mini%20128X64%20OLED%20LCD%20LED%20Display%20Module

Cheers
Douglas

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

DouglasPearless, 2019-07-22:
There are plenty like this on aliexpress :-)

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

vnguyen13, 2019-07-24:
Thanks @DouglasPearless! How did you wire the display?

DouglasPearless, 2019-07-25:
I will post a wiring diagram tomorrow on my GitHub site :-)

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

vnguyen13, 2019-07-25:
Great! I ordered one in so I will be able to try it out tonight. Just let me know which wire should go where and I'll test it out. Thank you @DouglasPearless!

DouglasPearless, 2019-08-02:
Sorry, I have been delayed as I need to print out an updated chassis and rewire it all.  I now have a new chassis and can wire it, then I will post all of that on my Github account :-)

Cheers
Douglas

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

Cblakslee, 2019-08-29:
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

I purchased the same OLED screen by mistake because the original was sold out. But mine remains pixelated no matter what. My wiring of the screen is the same as yours,

SDA -> Pin 3 (SDA), SCL -> Pin 5 (SCL), GND -> Pin 6 (GND), and VIN -> Pin 1 (3V3).

you said connecting the RST pin to GND, then running stats.py brought up the IP address. I run the command python3 stats.py and the terminal freezes. Please let me know if I am missing something. Thank you!

AustinPavlas, 2019-08-29:
@Cblakslee
I was never able to successfully get the OLED screen the work 100%.  I was able to get the screen to work flawlessly with another Nano that I had which was not using the Jetbot image.  Using a signal analyzer I was unable to find any differences between the two though.  In the end I was able to purchase the correct screen at a local electronics store and avoid any further headache.

Cblakslee, 2019-08-29:
> I was never able to successfully get the OLED screen the work 100%. I was able to get the screen to work flawlessly with another Nano that I had which was not using the Jetbot image. Using a signal analyzer I was unable to find any differences between the two though. In the end I was able to purchase the correct screen at a local electronics store and avoid any further headache.
@AustinPavlas
Ah, ok. That's what I was hoping not to resort too, but will for now for the same reason. Thank you for the response!

Closed 2022-07-15.

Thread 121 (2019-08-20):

Jetson doesn't turn on

Mundus131, 2019-08-20:
Hey.
Few moths ago I was writing about jetson which turns off while executing program . Now i have another big issue. I tried to use jetbot for detection and recognition road sign. I collected data, train AI and run program. At the begeinnig he recognised sign great and he was doing what i want, but after few sign he just turned off and now he doesn't want to turn on. All that time i was useing 10000mah xiaomi power bank. Now i even tried to power him up from phone charger but even that didn't helped me. I tried to disconnect camera, wifi adapter and no sign of life.

tokk-nv, 2019-08-21:
Hi Mundus131,
Sorry to hear you are experiencing some difficulty with the hardware.

The only thing I can think of as a potential cause to your issue was that the J48 header might be shortened with a jumper. If that is the case, the board is configured to take power only from the DC power jack and it will not take power from the Micro USB port.
Can you check if that happens to be the case?

If not, you may want to ask the same question on the Jetson Nano forum board.
https://devtalk.nvidia.com/default/board/371/jetson-nano/
There are NVIDIA support engineers on the forum who are more familiar with this kind of issue analysis, so you may have a better chance.

Mundus131, 2019-08-21:
No, there isn't any jumper at J48 header.
I just ordered recomended micro Usb power supply, which is 5,1V and 2,4 A. If it doesn't help I will ask the same question at NVIDIA support.
Thanks

jaybdub, 2019-08-22:
Hi Mundus131,

Thanks for reaching out!

It is possible that the Phone charger isn't capable of supplying the 5V@2A that Jetson Nano requires over micro USB.

Were you previously able to power using this phone charger, but now unable too?

Best,
John

Mundus131, 2019-08-25:
Hey John
Previously i was able to power using my power bank, but sometimes jetson turns off.
I used that new power supply and jetson turned on. When i disconnected power supply and power using power bank he also truned on. So now everything is fine.
Thanks

Closed 2019-08-28.

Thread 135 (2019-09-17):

I2C not working on jetbot

theacceloguy, 2019-09-17:
Hey,

I have been trying to get the motor driver installed , PCA9665 and lately been having the ERROR 12 - IO Error.

jasper@ubuntu:~$ sudo i2cdetect -y 0
Warning: Can't use SMBus Quick Write command, will skip some addresses
0 1 2 3 4 5 6 7 8 9 a b c d e f
00:
10:
20:
30: -- -- -- -- -- -- -- --
40:
50: -- -- -- -- -- -- -- -- -- -- -- -- -- -- -- --
60:
70:

Shows the same in sudo i2cdetect -y 1 and in sudo i2cdetect -y 2

The wiring is correct as i have tested the same sensor with same wiring on raspberry pi and they are working perfectly fine.
Tested the system, on recovery mode too and it gives the same error.
Also i did re-flashed the OS couple of times,and tried the same on the Jetson NANO OS. In all the cases i2C detect dosent works

Any help would be appreciated.

Thanks

jasper-hue, 2019-09-18:
[Update:]

I can find the devices on the console using the following command : i2cdetect -r -y
$ i2cdetect -y -r 1
     0  1  2  3  4  5  6  7  8  9  a  b  c  d  e  f
00:          -- -- -- -- -- -- -- -- -- -- -- -- --
10: -- -- -- -- -- -- -- -- -- -- -- -- -- -- -- --
20: -- -- -- -- -- -- -- -- -- -- -- -- -- -- -- --
30: -- -- -- -- -- -- -- -- -- -- -- -- -- -- -- --
40: 40 -- -- -- -- -- -- -- -- -- -- -- -- -- -- --
50: -- -- -- -- -- -- -- -- -- -- -- -- -- -- -- --
60: -- -- -- -- -- -- -- -- -- -- -- -- -- -- -- --
70: 70 -- -- -- -- -- -- --   

But still when i go and run  the basicmotion.py is executed the file shows error 121 : IO Error.

cagriy, 2019-10-10:
A bit late I suppose but is the PiOLED in the middle as described in the h/w setup page ? Maybe a good idea to test it without it to ensure it is not messing with any of the signals or power.

Otherwise, does the PiOLED working fine without motor driver ? Just to make sure Jetson is not faulty.

Finally, you mentioned that it was lately having this error, was it working before ?

TCIII, 2020-03-28:
@jasper-hue,
If you are using the recommended Adafruit DC Motor + Stepper FeatherWing Add-on its I2C address is not 0x40 like most servo driver boards that use the PCA9685 IC, but is 0x60. Hope that this helps.
I have used the Adafruit 16-Channel 12-bit PWM/Servo Driver in place of the Adafruit DC Motor + Stepper FeatherWing Add-on and have provided instructions here in the comments section of this [project](https://www.hackster.io/gatoninja236/building-a-custom-jetbot-with-jetson-nano-8d41b6)

Regards,
TCIII

Closed 2022-07-15.

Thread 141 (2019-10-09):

Minor change on chassis 3d model

aoqingy, 2019-10-09:
I hope to make a minor modification on chassis, for example, open four small hole on it. Is it possible to do this with .stl file?

Closed 2022-07-15.

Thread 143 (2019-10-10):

Unable to Properly flash SD image & Boot

rhklite, 2019-10-10:
I've tried many times to flash the [jetson nano SD card image](https://developer.nvidia.com/jetson-nano-sd-card-image-r322), however, unsuccessful. I'm out on ideas on what to do. Hoping to find some help here.

I'll describe my issue in chronological order.

1. Flashed [Sandisk 128gb](https://www.amazon.ca/gp/product/B073JYC4XM/ref=ppx_yo_dt_b_asin_title_o01_s01?ie=UTF8&psc=1) with [Etcher 1.5.57](https://www.balena.io/etcher/) for the first time. This SD card was freshly bought. I'm not sure if Etcher said successful or not after flash.
2. Connect Nano to HDMI and inserted the Sandisk SD card. Stuck on Nvidia logo.
3. looked at [this Nvidia dev forum post](https://devtalk.nvidia.com/default/topic/1052511/jetson-nano/jetson-nano-doesn-t-boot/). It seemed like people have mostly been fixing this problem with  1) new USB cable, 2) better power supply, 3) reflash image
4. Tried 2 different USB cable, and power supplies. (didn't work)
    1. Apple Charger (5.1v-2.1A),
    2. [Battery bank with 4.8A max current output](https://www.amazon.ca/Portable-Charger-Anker-PowerCore-20100mAh/dp/B00X5RV14Y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)
5. Tried reflash disk with Etcher. At this point i noticed Etcher failed to flash. the error is `Error: EIO: i/o error, write`
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
6. I open the SD card in Gparted, seeing the following 2 errors and a weird looking partition (shown in 3rd image). I figured this was due to the failed flash. So cleaned up the partition and formated the disk with the following procedure.
    1. In Gparted, deleted all partitions, declare new partitions and format to ext4.
    2. In gnome-disk or nautilist GUI, format the SD card again to ext4.
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
7. And at this point, **I figured I was stuck on Nvidia boot screen because the SD card image wasn't properly flashed** just started trying different combinations, variations. But the result is always the same. And it always leads to the same weird looking partitions in Gparted. I believe this error is not supposed to happen, since [jetson hack nano setup video](https://youtu.be/km0yT99eVTY?t=453) did not show this error
    1. Result 1: At 58% Etcher flash progress, write drops to 0, followed by  `Error: EIO: i/o error, write`. I reach this result if i perform step 6. then reflash
    2. Result 2: At 12% Etcher flash progress, write drops to 0, followed by  `Error: EIO: i/o error, write`. I reach this result if i did not perform step 6 before reflash. Sometimes after this step, Gparted i would see the entire SD card as unallocated in GParted, and GParted would say there is no partition Table. I then insert new partition table using `Gparted -> Device ->Created Partition Table`, then continue from there

8. The variations that I've tried.
    1. Etcher version 1.5.57,1.5.51
    2. Doing this on Windows vs Ubuntu 16.04
    3. Using zipped vs unzip SD card image
    4. New SD card, and new SD card adapter; Kingston 32GB
    5. Redownloaded the image
    6. Using SD card image [July release](https://developer.nvidia.com/jetson-nano-sd-card-image-r322) vs [Aug release](https://developer.nvidia.com/jetson-nano-sd-card-image-r3221)
    7. Different file system format: exFAT, NTFS, ext4
    8. Using `dd` on Command Line: gets error `dd: error writing '/dev/sda1': input/output error`

Any help would be really appreciated.

cagriy, 2019-10-10:
I wouldn't expect it to be related to the power supply. In the end this is not really a power hungry operation. Few ideas, although hard to tell without seeing it.

1 - New SD card adapter fine, did that come with its own new USB cable ?
2 - Might be a good idea to try a different USB port if this is available.
3 - Probably this is not the issue, but are you sure it is the SD card on /dev/sda1 ? Instead of your local hard disk :)
4 - What is your `sudo lsblk -o NAME,FSTYPE,SIZE,MOUNTPOINT,LABEL` output ?
5 - dd should work, below is how I did it on Mac, can you try this ?

Use lsblk or relevant command to confirm correct disk name
`sudo diskutil partitionDisk /dev/disk2 1 GPT "Free Space" "%noformat%" 100%`
`/usr/bin/unzip -p ~/Downloads/jetbot_image_v0p3p2.zip | sudo /bin/dd of=/dev/rdisk2 bs=1m`
(diskutil is a Mac command, please use equivalent command for linux)
your dd error mentions /dev/sda1 however, dd uses raw device, worth trying against /dev/rsda1 if this exists. Make sure you run dd as root, at least Mac requires root for this, perhaps linux wouldn't.

If nothing works, if possible try on another computer :)

rhklite, 2019-10-11:
@cagriy Thanks for the reply.

1. As for the adapter, i meant the microSD to SD sleeve. I didn't have a 2nd SD-USB/USB-C. I'm gonna buy a 2nd SD-USB adaptor to try this on.
2. Similar reason to 1. My adapter was a USB-C, and my computer only had one USB C port.
3. I'm sure of this, since all of my other hardrives are named /dev/nvme*
4.
with SD card plugin in
```
NAME        FSTYPE     SIZE MOUNTPOINT                                          LABEL
loop1       squashfs    89M /snap/core/7713                             
nvme0n1                477G                                             
├─nvme0n1p3 ext4     276.9G /mnt/storage                                        970 Pro
├─nvme0n1p1             16M                                             
└─nvme0n1p2 ntfs       200G /mnt/08C2120BC211FE1E                               970 Pro
loop17      squashfs   8.5M /snap/offlineimap/199                       
loop8       squashfs  35.3M /snap/gtk-common-themes/1198                
loop15      squashfs  54.5M /snap/core18/1192                           
loop6       squashfs 134.4M /snap/mathpix-snipping-tool/40              
loop13      squashfs  54.4M /snap/core18/1144                           
loop4       squashfs 193.1M /snap/mailspring/374                        
loop11      squashfs  42.8M /snap/gtk-common-themes/1313                
loop2       squashfs   8.4M /snap/offlineimap/210                       
loop0       squashfs 135.9M /snap/cloudcompare/200                      
loop9       squashfs 255.6M /snap/kde-frameworks-5-core18/30            
loop16      squashfs 193.3M /snap/mailspring/368                        
loop7       squashfs 420.9M /snap/pycharm-professional/154              
nvme1n1                477G                                             
├─nvme1n1p4 ntfs       900M                                                     WinRE tools
├─nvme1n1p2            128M                                             
├─nvme1n1p3 ntfs     107.6G /mnt/80608CC9608CC6FE                               Windows
├─nvme1n1p1 vfat       300M /boot/efi                                           SYSTEM
├─nvme1n1p8 ext4     346.4G /                                           
└─nvme1n1p6 ntfs      21.7G                                                     BIOS_RVY
sda                  119.1G                                             
└─sda1      ext4     119.1G /media/richard/dc21871e-9db4-434c-98b4-713f55f807eb
loop14      squashfs 260.7M /snap/kde-frameworks-5-core18/32            
loop5       squashfs 135.9M /snap/cloudcompare/197                      
loop12      squashfs 421.2M /snap/pycharm-professional/159              
loop3       squashfs  89.1M /snap/core/7917                             
loop10      squashfs 135.9M /snap/cloudcompare/198
```
without SD card plugined in
```
NAME        FSTYPE     SIZE MOUNTPOINT                       LABEL
loop1       squashfs    89M /snap/core/7713          
nvme0n1                477G                          
├─nvme0n1p3 ext4     276.9G /mnt/storage                     970 Pro
├─nvme0n1p1             16M                          
└─nvme0n1p2 ntfs       200G /mnt/08C2120BC211FE1E            970 Pro
loop17      squashfs   8.5M /snap/offlineimap/199    
loop8       squashfs  35.3M /snap/gtk-common-themes/1198
loop15      squashfs  54.5M /snap/core18/1192        
loop6       squashfs 134.4M /snap/mathpix-snipping-tool/40
loop13      squashfs  54.4M /snap/core18/1144        
loop4       squashfs 193.1M /snap/mailspring/374     
loop11      squashfs  42.8M /snap/gtk-common-themes/1313
loop2       squashfs   8.4M /snap/offlineimap/210    
loop0       squashfs 135.9M /snap/cloudcompare/200   
loop9       squashfs 255.6M /snap/kde-frameworks-5-core18/30
loop16      squashfs 193.3M /snap/mailspring/368     
loop7       squashfs 420.9M /snap/pycharm-professional/154
nvme1n1                477G                          
├─nvme1n1p4 ntfs       900M                                  WinRE tools
├─nvme1n1p2            128M                          
├─nvme1n1p3 ntfs     107.6G /mnt/80608CC9608CC6FE            Windows
├─nvme1n1p1 vfat       300M /boot/efi                        SYSTEM
├─nvme1n1p8 ext4     346.4G /                        
└─nvme1n1p6 ntfs      21.7G                                  BIOS_RVY
loop14      squashfs 260.7M /snap/kde-frameworks-5-core18/32
loop5       squashfs 135.9M /snap/cloudcompare/197   
loop12      squashfs 421.2M /snap/pycharm-professional/159
loop3       squashfs  89.1M /snap/core/7917          
loop10      squashfs 135.9M /snap/cloudcompare/198
```
5. i tried dd instruction from both the official setup page, and the instruction from stereo lab's page. None worked. I forgot why the version from the official setup page didn't work. But when i ran dd the second time following the stereo lab's page, i got `dd: error writing '/dev/sda1': input/output error`. And those two sets of cmd line instructions are pretty much the same.
6. Gonna try to find a new computer to try this with :(

rhklite, 2019-10-13:
resovled with new compute + new sd card adaptor

Closed 2019-10-13.

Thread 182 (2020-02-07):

Suggestion on improving JetBot/Jetson Nano performance

stevenlee090, 2020-02-07:
Hi All,

I have recently got a JetBot kit and was able to get assembled and software installed.
The examples run fine, but just seem a bit too sluggish compared to the videos linked in the Github Examples page.

For reference, I followed the instruction from https://github.com/NVIDIA-AI-IOT/jetbot/wiki/software-setup and setup everything using the `jetbot_image_v0p4p0.zip`.

However, I am not sure if it is the Jupyter Lab/Notebook which are slow or my routers or something with the JetBot, it just seems like there is significant delay (~1 second) in the camera video stream and also the control responsiveness of the JetBot.

Consequently, it is unable to avoid obstacles reliably, nor track an object reliably.
For obstacle avoidance, it often bumps into the obstacles first, then react 1-2 seconds later and starts turning left.
For object tracking, the gain had to be tuned to be much lower in order to avoid overshoot.

Therefore, I was wondering if there is anything I can try to help improve the performance of the JetBot / Jetson Nano.
Any advice or suggestions is appreciated.

kevindgoff, 2020-02-29:
The latency issues improved for me once I switched to a Wi-Fi module vs a usb version. there is still a slight delay but the bot reacts better now.

stevenlee090, 2020-02-29:
@kevindgoff thanks for the feedback. I actually have the Intel wifi module which is recommended in the bills of materials for the JetBot. Someone else mentioned to me that it could be the SD card which is the processing bottleneck for me, but I haven't had the chance to try out a faster card yet.

Have you tried different SD cards with your Jetson Nano by any chance?

stevenlee090, 2020-03-10:
Upgraded my SD card to a UHS-I class one, but the demo programs still feel kind of sluggish. Not sure what I was missing.

dmccreary, 2020-03-15:
I am having the same issues.  Perhaps Jupyter and Python is just too slow for real-time robotics.  I am also evaluating the DonkeyCar and it seems much, much faster!

jaybdub, 2020-03-15:
Hi All,

Thanks for reaching out and sharing your experience!

I have not personally witnessed this in my testing, it could be some regression in our latest v0.4.0 JetBot image.  When developing JetBot, we noticed that even when network latency was bad (video not streaming to Image widget), the robot was still able to respond in real time.  Certainly not 1-2 seconds, I feel there is a different issue.

Do you mind sharing the following information

* Which example notebook is causing issues
* Which JetBot are you using (is it the open-source, or third party)
* Which WiFi module are you using
* Do you experience the issue when using the previous v0.3.2 JetBot image?

Hope I can help get past this!

Best,
John

stevenlee090, 2020-03-16:
@jaybdub Thanks for getting back to this issue.

Below is the information for my use case:
* The notebooks which I am facing issues with are the **obstacle avoidance notebook** and the **object following notebook**. As described previously, the notebooks do seem to work, but there exhibits a certain amount of delay which causes the demo to be really sluggish.
* I am using an open-source JetBot with 3D printed chassis, third party motors and motor controller. It was a kit as shown in this [video](https://www.youtube.com/watch?v=ADqLbs_xAlg). There might be some slight difference hardware, but I did not think they would be enough to cause a problem like this.
* I am using the `M2 Intel Wireless-AC 8265` module as suggested in the bills of materials.
* I have actually only tested with the latest image `v0.4.0` and not the previous JetBot image. This might be worth a try actually.

So in my case, there is some hardware variation being that the motor and motor driver are not the offiical Adafruit version, but I doubt this is the root cause (not ruling it out at the moment though).

Thanks for mentioning about flashing an earlier version, this is indeed worth a shot.
I will try that once I finish my current development on the JetPack image, and will try to re-flash to the earlier version.

stevenlee090, 2020-03-16:
@dmccreary I still feel like Jetson Nano is capable enough to do real-time robotics. It just depends on the machine learning models you are trying to deploy and how well your program is optimized. For instance, the Nano is capable of reaching 10-20 fps with `YOLOv3-tiny` which is really quite impressive for such a small form factor.

Had a quick look at the donkey car, it does seem pretty cool!

StefanW0815, 2020-05-05:
I had the same problem: JetBot was simply not able to follow any kind of road, even under best optical conditions like bright "street" on dark floor. I mixed some code from the data collection to display the target direction marker and you could see that it wanted to go to the center of the street. But it constantly overshot because of lag in the system. There are also several seconds lag between scene in front of jetbot and PC update.
When a monitor is connected, the task manager of the jetbot shows both CPUs running close to 100%. The jetbot simply doesn't seem to be able to handle the load. I set the camera to 10Hz and the CPU load dropped a bit and at least the lag reduced.
But the final solution was getting a fan and bumping up the power to max. With all 4 CPUs running the load dropped to ~50%. But the road follow example did only work smooth when the camera was set to 10fps on top of max power.
Just to add, my laptop is a brand new Alienware which should not be a bottleneck. I run Ethernet via cable and created a mobile hotspot with the jetbot directly communication to the laptop. This way there is no interference with any WiFi traffic.

xiepan610, 2020-05-13:
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

Hi！ Could you tell me how to set the camera to 10fps ?

StefanW0815, 2020-05-13:
#camera = Camera()
camera = Camera.instance(width=224, height=224, fps=10)

I replaced the Camera instantiation in data_collection and in live_demo to get a reasonable update.

xiepan610, 2020-05-14:
@StefanW0815 Thank you very much！I‘ve also receive your  E-mail.

tomMEM, 2020-06-21:
One possibility would be to try the different power modes of the jetson as previously mentioned:
sudo /usr/sbin/nvpmodel -q                  -  will show current power mode
sudo jetson_clock --show                      - will show current power mode with more details
Output should be: GPU MinFreq=76800000 MaxFreq=921600000 CurrentFreq=921600000
CPU0-3 active: MaxFreq=1479000 CurrentFreq=1479000
If not then try:  sudo /usr/sbin/nvpmodel -m 0  or 1
or sudo jetson_clock.

tomMEM, 2020-07-04:
Update to my previous message: sudo jetson_clocks to get MaxFreq is only possible if nano is connected to the 4A input from a respective power bank (e.g. Oppo).

However, whereas it helped to have MaxFreq in the collision_avoidance example, the problem with a time lag in object_following example remained.
The delay (1-3sec) comes from the line  "detections = model(image)"  in the object_following live_demo script (last JetBot SD image May 2020, B01 nano).
Thus, the object recognition seems to have lost on speed in a newer version.
Would be great to get additional suggestions. Best. T

abuelgasimsaadeldin, 2020-08-25:
Hi StefanW0815,

you mentioned that you mixed some codes from the data collection to display the target direction marker while running the live demo, may I please know what exactly are these codes? I want to know if my training model is the problem for my road following not achieving the expected results or it is something else and I am really new to coding in general. Thanks in advance.

tomMEM, 2020-08-25:
Hello, you could add to the camera cell the code from data_collection of road following project (below camera()).

I added already to the script at https://github.com/tomMEM/Jetbot-Project live_demo_roadfollowing_targetdisp.ipynb
and also add joystick movement to data_collection_joystick_roadfollowing.ipynb - you could try.
However, so far I was not successful to have the bot following the line - the x y coordinates are way outside of the band and steering is way to strong.

For more complex road following systems, you might have a look at https://atsushisakai.github.io/PythonRobotics/
"Path tracking"

abuelgasimsaadeldin, 2020-08-26:
Hi tomMEM,

thanks for the reply I managed to make my road following example work by adjusting the speed of the motors as the reason for not achieving the expected results was found to be due to the motors not operating at the same speed, but still it will be nice to see the target direction marker while running the live demo.

Now I am trying to combine this road following together with collision avoidance, not sure if there are available codes online for that already and if so it would be very helpful indeed.

calleliljedahl, 2021-08-29:
> The latency issues improved for me once I switched to a Wi-Fi module vs a usb version. there is still a slight delay but the bot reacts better now.

thanks - will try

Closed 2022-07-18.

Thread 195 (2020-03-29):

jetson not booting with jetbot image

ndpeach, 2020-03-29:
I'm not able to boot the jetson with the jetbot SD image, no activity on the monitor. The Jetson nano powers up but there's nothing on the monitor which I've connected to the DP and the HDMI ports.

I'm able to boot the jetson nano from the normal development kit SD card image but not the jetbot images, I've tried both jetbot_image_v0p3p2 and jetbot_image_v0p4p0 and the same effect.

I've tried powering it from the 4A 5v barrel connector and via the battery / motor board in the jet bot kit, both the same result.

I've tried etcher from windows and mac with no difference, it's a 64 GB samsung SD card.

Any advice apprecaited.

TCIII, 2020-03-29:
@ndpeach,

Did you complete this instruction in the software setup:

ndpeach, 2020-03-29:
hi, thanks for your reply, yes, though in my case, I'm using the 5v 4amp barrel connector for power instead of the micro USB. Would that make a difference?  I'm following these https://github.com/NVIDIA-AI-IOT/jetbot/wiki/software-setup and got as far as step 2

TCIII, 2020-03-29:
@ndpeach,

I assume that you have jumper 48 installed to use the barrel power jack?

This is strange as I have had no problems using  jetbot_image_v0p4p0.zip. Did you verify the down load before you unzipped it? I always test before unzipping then use Etcher to burn the image to the SD card (San Disk 64GB Ultra Plus)

Regards,
TCIII

ndpeach, 2020-03-30:
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

Hi, thanks again for your reply, yes, the jumper is on, I've not unzipped this and find that I can't unzip it, it looks like it's the download that is the problem, thanks for the input.

ndpeach, 2020-03-30:
hi, I've attempted to download this several times, certainly, it's causing archiver on mac and 7zip on windows to throw up errors about the zip file being corrupt, is this to do with it being on google drive, is it available somewhere else?

ndpeach, 2020-03-30:
I've now tried with the command line utilities for both mac and linux and I get the same message about a corrupt zip. here's the command and it's output, I'm just trying to see if the file will unzip.

➜  Downloads /usr/bin/unzip -p jetbot_image_v0p4p0_2.zip
[jetbot_image_v0p4p0_2.zip]
error: End-of-centdir-64 signature not where expected (prepended bytes?)
  (attempting to process anyway)
warning [jetbot_image_v0p4p0_2.zip]:  1055073 extra bytes at beginning or within zipfile
  (attempting to process anyway)
file #1:  bad zipfile offset (local header sig):  1055073
  (attempting to re-compensate)
file #1:  bad zipfile offset (local header sig):  1055073

is this file available anywhere other than google docs ? Thanks

ndpeach, 2020-03-30:
quick update, downloaded the latest zip via a linux machine, this time it's complete and not generating faults with unzip, I've been able to use etcher on linux to then copy the image to my SD card and all looks good.

Closed 2020-03-30.

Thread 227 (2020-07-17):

Link motors to traitlets - Jetbot

ai-hengineer, 2020-07-17:
I’m trying out Jetbot example 1 (basis_motions.ipynb) on my Sparkfun Jetbot.
The motors are working well when set «directly» through methods: left, right, forward, backward.
However, when linking the motors to widgets using traitlets (using the example), the motor does not move.
Does anyone have a solution for this?

santaimpersonator, 2020-08-05:
For the SparkFun Jetbot:

With the traitlets, the motors should be controlled by the [motor.py](https://github.com/sparkfun/jetbot/blob/master/jetbot/motor.py) file. I just tested a fresh v01-10 image on a Jetson Nano (with the one camera connector carrier board), but didn't have issues.

1. Did you link the traitlets multiple times? I can't remember, but I think this was a little finicky and you had to link it either once or twice for the traitlets to work.
2. Let's try to double check the motor driver is recognized. Enter the following in a terminal: `i2cdetect -y -r 1`. You should see an address listed at `5D`. If not, you may need to double check that the Qwiic cable.
3. Let's check how the motor driver is configured (you if you could check this at various points; it would help to find where the code might be breaking). Enter the following in a terminal: `i2cdump -y -r 1 0x5D`.
    * At register `SCMD_STATUS_1 = 0x77` you will see:
        * `0`: When the motor driver is ready.
        * Greater than `0`: When the motor driver is enumerating or busy.
    * At register `SCMD_DRIVER_ENABLE = 0x70` you will see:
        * `0`: When the motor driver is disabled.
        * `1`: When the motor driver is enabled.
    * At register ` SCMD_MOTOR_A_INVERT = 0x12` and `SCMD_MOTOR_B_INVERT = 0x13` you will see:
        * `0`: When the motor driver direction is not inverted.
        * `1`: When the motor driver direction is inverted.
    * At register SCMD_MA_DRIVE = 0x20` and `SCMD_MB_DRIVE = 0x21` you will see:
        * `0x80`: When the motor driver speed is set to `0`.
        * <`0x80`<: When the motor driver direction is not `0`.
4. Let's see if there might be something weird happening in the code between the two cells:
    1. Try restarting and clearing the kernel.
    2. Then, implement the `from jetbot import Robot` cell.
    3. Skip the `robot.left(.3)` `time.sleep(.5)` `robot.stop()` cell.
    4. Proceed on to the widget and traitlet linking cells.

santaimpersonator, 2020-10-09:
@ai-hengineer If this issue has been resolved please close this issue.

Closed 2022-07-15.

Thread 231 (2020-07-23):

AttributeError: 'Motor' object has no attribute '_motor'

VegardIversen, 2020-07-23:
Hi
Im suddenly getting this error when running robot.stop():
 ```
Error in atexit._run_exitfuncs:
Traceback (most recent call last):
  File "/usr/local/lib/python3.6/dist-packages/jetbot-0.3.0-py3.6.egg/jetbot/motor.py", line 60, in _release
    self._motor.disable()
AttributeError: 'Motor' object has no attribute '_motor'
```
Any suggestions on how to fix?

jaybdub, 2020-07-23:
Hi VegardIversen,

Thanks for reaching out!

Are you using one of the JetBot SD card images, or perhaps a third party JetBot with a different set of instructions?

If you're using a third party bot, do you mind sharing the instructions you followed?

Best,
John

VegardIversen, 2020-07-23:
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

Hi
Thank you for quick replay. Im using the image from this kit [https://learn.sparkfun.com/tutorials/assembly-guide-for-sparkfun-jetbot-ai-kit/all](url). T
The weird thing is that it worked before.

jaybdub, 2020-07-23:
Hmm, strange.

Did you update or modify the software at all?

If not, I would suspect it is a hardware issue.  Perhaps the motor driver connection came loose, and is not discoverable.

You can use the i2cdetect tool to see if the motor driver is discoverable.

Do you mind sharing the output of the following

```bash
sudo i2cdetect -y 1
```

Best,
John

VegardIversen, 2020-07-24:
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

I have just updatet opencv. Motors seems to work driving forward, but gets an error when using robot.stop() and they dont drive the correct duration.

This is the output from the command:
Warning: Can't use SMBus Quick Write command, will skip some addresses
     0  1  2  3  4  5  6  7  8  9  a  b  c  d  e  f
00:                                         
10:                                         
20:                                         
30: -- -- -- -- -- -- -- --                 
40:                                         
50: -- -- -- -- -- -- -- -- -- -- -- -- -- 5d -- --
60:                                         
70:

santaimpersonator, 2020-08-05:
Hey there, you seem to be having an issue similar to another user on the [SparkFun forum](https://forum.sparkfun.com/viewtopic.php?f=88&t=53479).

I just tested this out on our newer v01-10 image and with a Jeston Nano (with the one camera connector carrier board), but I wasn't able to duplicate the issue. Did you happen to modify the files at all? Here is a link to our [fork of this repo](https://github.com/sparkfun/jetbot) for a reference.

If you accidentally modified the files, you can follow these instructions for building a card from scratch: https://github.com/NVIDIA-AI-IOT/jetbot/wiki/Create-SD-Card-Image-From-Scratch
* Start from step 9, but use the link to our repo instead of cloning Nvidia's.
* If you clone Nvidia's repo, you will run into issues because of the hardware difference.

VegardIversen, 2020-08-06:
Hey, that is also my post. The error are just showing up after a program has run, and not during so its not breaking the system anymore. I will try with new hardware on another unit soon, and can see if that fixes the problem.

santaimpersonator, 2020-08-06:
As you mentioned that the code worked previously, it definitely leads me to believe that something has changed in either the `motor.py`, `robot.py`, or the `basic_motion.ipynb` files. However, now that you are saying, "the error are just showing up after a program has run, and not during so its not breaking the system anymore," I am a little confused to how that method is getting called/implemented. Is this for a custom code/script and not one of the example notebooks provided for the Jetbot?

VegardIversen, 2020-09-24:
both custom and example notebook gets the error

santaimpersonator, 2020-09-24:
I recently updated SparkFun's fork; there was an incorrect class name in that method:
https://github.com/sparkfun/jetbot/commit/1453860b99149a89b6150567e75fd656748eb548

santaimpersonator, 2020-10-09:
@VegardIversen Are you still getting the error message?

VegardIversen, 2020-10-09:
> @VegardIversen Are you still getting the error message?

Yep

VegardIversen, 2020-10-09:
@santaimpersonator yep

santaimpersonator, 2020-10-09:
Have you pulled the fork or modified the file directly as mentioned in the commit (https://github.com/sparkfun/jetbot/commit/1453860b99149a89b6150567e75fd656748eb548)? It should resolve the issue.

VegardIversen, 2020-10-09:
No, but I dont have access to the robot anymore, but i guess that would fix it. I have no way of testing it now..

santaimpersonator, 2020-10-09:
Fair enough. In that case, would you mind closing this issue for now.

If you ever get a hold of the robot again and run into the issue, you can reopen this issue. I'd be happy to assist you again.

seeeheng, 2021-02-04:
> Have you pulled the fork or modified the file directly as mentioned in the commit ([sparkfun@1453860](https://github.com/sparkfun/jetbot/commit/1453860b99149a89b6150567e75fd656748eb548))? It should resolve the issue.

Hi @santaimpersonator -

I had the same error message, and I can confirm that changing line 60's `self._motor.disable()` to `self._driver.disable()` resolves the issue. Seems like it was a simple attribute naming error haha.

Thanks for the help!

santaimpersonator, 2021-02-04:
@seeeheng Thanks for the feedback.
@jaybdub I think this issue is resolved and can be closed.

Closed 2022-07-15.

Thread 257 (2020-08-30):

Pioled screen not working on my jetbot

shanunrandev123, 2020-08-30:
im working on jetson TX2 and building a Jetbot,but the pioled screen is not showing the ip address,i have checked all the hardware connections

jaybdub, 2020-09-01:
Hi @shanunrandev123 ,

Thanks for reaching out!

I haven't personally tested the PiOLED on the Jetson TX2 yet.  Perhaps there was an issue with permissions.

Since you're not starting from the base JetBot image, do you mind sharing what steps you've taken to configure your system and run the IP address display script?

Best,
John

shanunrandev123, 2020-09-01:
Well, firstly I flashed that latest jetbot image on my sd card using etcher, everything was working well,the oled was showing the ip address but suddenly the voltage tripped and internet connection got lost and there was no display.I tried to Reboot the system again but failed.,I tried to boot Jetson nano again w/o connecting the motor driver but still there wer no results

jaybdub, 2020-09-01:
Hi shanunrandev123,

Just to clarify, are you using a Jetson TX2, or did you mean Jetson Nano in your original post?

I'm sorry to hear the issue, hopefully nothing was broken.  The first thing I would try in this scenario would be to see if it works from wall power and monitor, without anything connected  (even the PiOLED), from a standard Jetson SD card image.  Once we've verified the Jetson Nano is working as usual we could move forward addressing the JetBot specific components.  Be sure to apply 5V when applying to the Jetson Nano directly (I believe some 3rd party kits include 12V chargers for the robot breakout board, which regulates down to 5V, so don't apply that directly to Jetson if that is the case for you).

Please let me know if this helps, or if I'm perhaps misunderstanding the situation.

Best,
John

Closed 2022-07-15.

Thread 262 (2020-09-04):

[SOLVED] Camera Blank - using sep 2020 clone

tomMEM, 2020-09-04:
Hello, I lost my SD installation, so I started with the last SD-Image and a fresh clone of jetbot again.

Unfortunately the Camera gives blank (empty) images which led to OpenCV errors - "empty images cannot be processed".
I replaced the very last Camera.py with an old Camera.py (beginning august 2020) and scripts work again.

Please check how to proceed. The camera settings are now in opencv_gst_camera.py, but there seems to be no links to it
Thanks. T

jaybdub, 2020-09-04:
To answer your question around passing parameters using current state of master you can do

```python
from jetbot.camera.opencv_gst_camera import OpenCvGstCamera

camera = OpenCvGstCamera(width=224, height=224)
```

tomMEM, 2020-09-05:
Hello John, thank you for the fast response.
Adding the “from jetbot.camera.opencv_gst_camera import OpenCvGstCamera” and “camera=....” into the cell of the first Camera call of any script worked nicely.

Using git checkout v0.4.0 also helped to resolve the camera issue, however, I had to delete, re-clone the repository and git checkout v0.4.0, because I modified the camera.py before, and I am not sure how to handle the git stash tool.

Thanks again. Best. T

jaybdub, 2020-09-05:
Nice glad to hear it's working for you!

FYI we actually just patched master so you can go back to

``camera = Camera(width, height)``

Also, it won't be needed here, but in case it helps you in the future, I believe the flow for [git stash](https://git-scm.com/docs/git-stash) is

1. ``git stash`` to undo your changes in your working directory since the last commit and store them in the background
2. ``git checkout ...`` to switch working directory to some other commit
3. ``git stash pop`` to pull your changes out of storage and apply them to the current working directory

This wont do any commits to the repository.  If you test it out, calling ``git status`` before/after each command should help demonstrate what's happening.

Please let me know if you run into any other issues.

Best,
John

tomMEM, 2020-09-05:
Hello John, thank you for the stash info that might become handy.
The last repository (06092020) is working.
I had problems to get back the old bot performance.

It looks like the SD image does not allow to use "$sudo jetson_clocks" to switch to Max power, even the fan goes to Max speed, which gave the wrong impression of all four CPUs working, but actually only the CPU frequency goes up. Sure, it is written at many places, but it is easy to miss, and somehow before jetson_clocks was sufficient.

Using $sudo jtop that is preinstalled on the SD image, Max power can be activated ($sudo nvpmodel -m 0  for 10 W.)
I am not sure if jetson_clocks controller need to be activated too.
Time lag of trt roadfollowing display is back to less than a second.
Thanks again.
Best. T

jaybdub, 2020-09-08:
Awesome, thanks for the information.  It may help for us to document these power configuration details more thoroughly.

Out of curiosity, are you using the open source JetBot?  If so which WiFi module are you using, the M2 module or a USB dongle?

Best,
John

tomMEM, 2020-09-09:
Hello John, the bot system is a buy-by-pieces, however, recommended nano hardware was chosen.
The Wifi hardware is based on an Intel 8265/8275 (ver 78) installed at M2.
The laptop is connected to the bot over an Android phone using the Hotspot function.
However, regarding time lag, it seems not to make a difference, which type of the three connections is chosen, at least at the level of visual perception.
Best.
T

Closed 2020-10-11.

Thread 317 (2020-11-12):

Module Not Found Error

spy-maker, 2020-11-12:
Hi,
I am working on jetpack version 4.4 from scrath when I ran notebook codes I am keep getting No module named 'jetbot' error. Does anyone know how to fix this ?
I also keep getting same error for Adafruit.

jaybdub, 2020-11-16:
Hi spy-maker,

Thanks for reaching out!

This error indicates the jetbot package is not installed.  Do you mind sharing the steps you followed, as well as the commands which produced these errors?

Best,
John

spy-maker, 2020-11-16:
Previously I was using jetpack version 4.3 of another image. Due to the limitations I switched to 4.4 jetpack version. After I download the jetpack image from Nvidia website and used docker to download jetbot. I also downloaded the adafruit modules from online and after the setup it works but I couldn't fix this jetbot module issue.

So right now I am wondering whether I should try flash the new jetbot image with 4.4 jetpack version instead of using docker. And is there any specific steps to download jetbot modules?

Normally after I flash the image I will setup things such as:
- apt update & upgrade
- download deep learning framework

I also wanted to check is there any other steps for setup this ?

jaybdub, 2020-11-16:
Hi spy-maker,

FYI, flashing the latest _JetBot_ image actually wraps the docker container.   Because of this, the new JetBot image may not help here.  There has been some frustration with this docker update in the community, which it sounds like your use case resonates with.  Please let me know if you have any feedback on this, or ideas on what you _expect_ to see from the JetBot SD card image.  This will help inform our judgment.

To install on a native configuration, there are a few steps.

1.  Install software dependencies.
    1.  The main one is PyTorch, you can find it here https://forums.developer.nvidia.com/t/pytorch-for-jetson-version-1-7-0-now-available/72048
    2.  Many other dependencies can be installed by referencing the base docker file https://github.com/NVIDIA-AI-IOT/jetbot/blob/master/docker/base/Dockerfile#L72

After the software dependencies are installed, you should be able to import the JetBot library.  To get the JetBot development experience, you will need to configure the system to launch the Jupyter lab server at boot.

Please let me know if this helps or you run into issues installing the software dependencies, and I'm happy to help with instructions for getting the Jupyter lab server running.

Best,
John

spy-maker, 2020-11-17:
Dear John,
I have flashed new jetbot image with jetpack version 4.4.1 directly into the sd card instead of using docker method. Is it possible for you to guide me on how to setup things after I flash new sd card image?

Especially the jetbot modules part.
Regards,
Karthick

hex0r, 2020-11-18:
Hi everyone,

I have an question regarding jetbot modules and jupyter. I had to change the robot.py due to custom motor driver but now i have the following issue if I execute the basic_motion notebook

OSErrorTraceback (most recent call last)
<ipython-input-2-b418ad9f6ab3> in <module>
----> 1 robot = Robot()

/usr/local/lib/python3.6/dist-packages/jetbot-0.4.1-py3.6.egg/jetbot/robot.py in __init__(self, *args, **kwargs)
     20     def __init__(self, *args, **kwargs):
     21         super(Robot, self).__init__(*args, **kwargs)
---> 22         self.motor_driver = Adafruit_MotorHAT(i2c_bus=self.i2c_bus)
     23         self.left_motor = Motor(self.motor_driver, channel=self.left_motor_channel, alpha=self.left_motor_alpha)
     24         self.right_motor = Motor(self.motor_driver, channel=self.right_motor_channel, alpha=self.right_motor_alpha)

The error itself is not the problem because I dont use motor_hat but this is not the same code as in my robot.py.
I already deleted the /usr/local/lib/python3.6/dist-packages/jetbot-0.4.1-py3.6.egg/jetbot/robot.py and add the fowling code at the beginning

import sys
import importlib
sys.path.insert(0, '/home/jetbot/jetbot')
from jetbot import Robot

If is use runipy ./notebooks/basic_motion/basic_motion.ipynb everthing works as expected.
What is the different to jupyter
tried  to reboot, shutdown kernels..
and how can jupyter read the  old /usr/local/lib/python3.6/dist-packages/jetbot-0.4.1-py3.6.egg/jetbot/robot.py even it is already deleted.
I am not an python expert, so can anybody give me an hand please??
thx

spy-maker, 2020-11-19:
Hi John,
I tried flashing jetbot image directly instead of using docker and it works well this time. I didn't encounter jetbot module issue this time. Currently, I am setting up this jetpack 4.4.1 version using my customised jetbot. Previously I was working on it using 4.3. So right now, I am setting up this to make it run. I already have the required files needed but I am getting errors.

I want to get clarify few things:

1) After I flashed the new image I modified pioled display code to make it work. I changed **i2c to 0** and it works well. Later I created display service to make it auto run after every time it boot up. It only display ip address after I enter the password is there any ways to fix this. Do I need to create Jupyter service ?

2) Like I mentioned earlier I already have required modules and drivers needed to run but I dont know how to setup those because I already have those modules installed. Can you help me with this ?
I need to setup adafruit motor, servo, gpio and Rpi.

I am unable to setup and configure those mentioned above and it resulted to errors when I run codes. I am getting **os error error no 121 Remote I/O error**

spy-maker, 2020-12-14:
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

Try using the old jetbot module which was used previously for training. I flashed new jetpack version and installed required drivers and for the modules try using the old version. For example I am using jetbot 0.3.0 previously but when I used 0.4.1 I get this issue so try switching back to previous version.

Closed 2020-12-14.

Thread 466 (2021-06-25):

Determine storage location of Adafruit_MotorHAT library package in Jetbot v 0.4.3

TCIII, 2021-06-25:
Need a little assistance here:

The Jetbot v 0.4.3 image communicates with the FeatherWing Motor Controller board using the Adafruit_MotorHAT library. Prior to Jetbot v 0.4.3 the Adafruit_MotorHAT library package was stored at “/usr/local/lib/python3.6/dist-packages/Adafruit_MotorHAT-1.4.0-py3.6.egg/Adafruit_MotorHAT/Adafruit_MotorHAT_Motors.py” The Jetbot v 0.4.3 image no longer stores the Adafruit_MotorHAT library package at that location as “/usr/local/lib/python3.6/dist-packages/" is empty in the Jebot v 0.4.3 image.
Therefore I would like to know where the Jetbot v 0.4.3 image is storing the Adafruit_MotorHAT library package sol that I can adjust the PCA9685 servo board’s PWM switching frequency as I have stated above.

Reply
cancel

TCIII, 2021-06-25:
I have received the following from Adafruit Customer Service:

That library is deprecated and has been archived:
https://github.com/adafruit/Adafruit-Motor-HAT-Python-Library

The new library is here:
https://github.com/adafruit/Adafruit_CircuitPython_MotorKit

Install info in guide here:
https://learn.adafruit.com/adafruit-dc-and-stepper-motor-hat-for-raspberry-pi/installing-software

Comments?

santaimpersonator, 2021-06-28:
As of last week, I didn't have issues installing the jetbot package (includes installation of Adafruit Motor Hat package) with the [setup.py script](https://github.com/NVIDIA-AI-IOT/jetbot/wiki/Software-Setup#step-5---install-latest-software-optional) or with the [Docker containers](https://github.com/NVIDIA-AI-IOT/jetbot/tree/master/docker).

TCIII, 2021-06-28:
@santaimpersonator,

I never had a problem either installing Jetbot from the latest Nano 4GB image, but that is not the subject of this issue.

You will notice that Adrafruit_MotorHAT is deprecated and therefore needs to be replaced with the Adafruit_CircuitPython_MotorKit library as advised above.

However, I digress. All I want to know is the following:

"The Jetbot v 0.4.3 image communicates with the FeatherWing Motor Controller board using the Adafruit_MotorHAT library. Prior to Jetbot v 0.4.3 the Adafruit_MotorHAT library package was stored at “/usr/local/lib/python3.6/dist-packages/Adafruit_MotorHAT-1.4.0-py3.6.egg/Adafruit_MotorHAT/Adafruit_MotorHAT_Motors.py” The Jetbot v 0.4.3 image no longer stores the Adafruit_MotorHAT library package at that location as “/usr/local/lib/python3.6/dist-packages/" is empty in the Jebot v 0.4.3 image.
Therefore I would like to know where the Jetbot v 0.4.3 image is storing the Adafruit_MotorHAT library package sol that I can adjust the PCA9685 servo board’s PWM switching frequency."

santaimpersonator, 2021-06-29:
To clarify:
- The installation steps and Python package work fine. Therefore, it isn't necessary to utilize the other package.
    - It sounds like *maybe* want to file an issue about utilizing the new Python package (that isn't deprecated) instead
- Additionally, I was showing you how the packages got installed (to point you in the right direction).

That being said...
- It sounds like previously, you used this repo as a Python package (via the [setup.py script](https://github.com/NVIDIA-AI-IOT/jetbot/wiki/Software-Setup#step-5---install-latest-software-optional)), which installs the Adafruit package with the rest of the Python packages.
    - If you aren't familiar with Python, the files may also be in the hidden local folder of the home directory.
    - I'm fairly confident that when packages are installed the printout tells you where they area located, as well.
- The recent Jetbot implementations use Docker containers to create their own "virtual workspace".
    - You can modify the files from within the Docker container, but any changes you make will not be permanent.
        - The location of the "virtual workspace" Python files will be similar to OS
    - For reference, the [setup.py script](https://github.com/NVIDIA-AI-IOT/jetbot/wiki/Software-Setup#step-5---install-latest-software-optional) still installs the Adafruit Python packages for the docker container: https://github.com/NVIDIA-AI-IOT/jetbot/blob/master/setup.py#L20

*Good luck making all the necessary changes to utilize the new Adafruit package. You'll want to make all you code changes before [building and enabling your container](https://github.com/NVIDIA-AI-IOT/jetbot/tree/master/docker).*

TCIII, 2021-06-29:
@santaimpersonator,

You have totally missed the point.

If you install the Jetbot IMAGE from [here,](https://github.com/NVIDIA-AI-IOT/jetbot/blob/master/docs/software_setup/sd_card.md) there are no "packages" to watch being built and installed as the required Jetbot packages/modules are already in the IMAGE.
You need to understand the difference between a prebuilt Jetbot IMAGE and an installation of Jetbot built from SCRATCH by the user which I did not have to do in this case.
When I first used Jetbot, I had to first install Jetpack and then follow a guide to install the required Jetbot packages and modules.
Example: I have built Jetrace from scratch using these [instructions](https://github.com/NVIDIA-AI-IOT/jetracer/issues/89) and as a completed image found [here](https://github.com/NVIDIA-AI-IOT/jetracer/blob/master/docs/software_setup.md) so I know all about installations from scratch and from images.

TCIII, 2021-06-29:
@santaimpersonator,

You didn't bother to read my response at all, probably stopping at "my response was pointless" as you obviously do not know the difference between an installed image of Jetbot and an Jetbot installation built from scratch.

Docker has nothing to do with my issue and therefore you have nothing to bring to the table to address my issue.

TCIII, 2021-07-06:
@santaimpersonator,

Okay, I was able to get to where "Adafruit_MotorHAT_Motors.py" is in the jetbot workspace using the Jupyter terminal.

However, how can I edit "Adafruit_MotorHAT_Motors.py" as gedit only works in the Desktop mode and there is no nano editor in the workspace?

Closed 2021-07-06.

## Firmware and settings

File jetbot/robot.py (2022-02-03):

# Modified by SparkFun Electronics June 2021
# Author: Wes Furuya
#
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
#==================================================================================
# Copyright (c) 2021 SparkFun Electronics
#
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
# THE SOFTWARE IS PROVIDED "AS IS", WITHOUT WARRANTY OF ANY KIND, EXPRESS OR
# IMPLIED, INCLUDING BUT NOT LIMITED TO THE WARRANTIES OF MERCHANTABILITY,
# FITNESS FOR A PARTICULAR PURPOSE AND NONINFRINGEMENT. IN NO EVENT SHALL THE
# AUTHORS OR COPYRIGHT HOLDERS BE LIABLE FOR ANY CLAIM, DAMAGES OR OTHER
# LIABILITY, WHETHER IN AN ACTION OF CONTRACT, TORT OR OTHERWISE, ARISING FROM,
# OUT OF OR IN CONNECTION WITH THE SOFTWARE OR THE USE OR OTHER DEALINGS IN THE
# SOFTWARE.
#==================================================================================

import time
import traitlets
from traitlets.config.configurable import SingletonConfigurable
import qwiic
from Adafruit_MotorHAT import Adafruit_MotorHAT
from .motor import Motor

# Scan for devices on I2C bus
addresses = qwiic.scan()

class Robot(SingletonConfigurable):

    left_motor = traitlets.Instance(Motor)
    right_motor = traitlets.Instance(Motor)
    
    
    # config
    i2c_bus = traitlets.Integer(default_value=1).tag(config=True)
    left_motor_channel = traitlets.Integer(default_value=1).tag(config=True)
    left_motor_alpha = traitlets.Float(default_value=1.0).tag(config=True)
    right_motor_channel = traitlets.Integer(default_value=2).tag(config=True)
    right_motor_alpha = traitlets.Float(default_value=1.0).tag(config=True)

    # Adafruit Hardware
    if 96 in addresses:
            
            def __init__(self, *args, **kwargs):
                super(Robot, self).__init__(*args, **kwargs)
                self.motor_driver = Adafruit_MotorHAT(i2c_bus=self.i2c_bus)
                self.left_motor = Motor(self.motor_driver, channel=self.left_motor_channel, alpha=self.left_motor_alpha)
                self.right_motor = Motor(self.motor_driver, channel=self.right_motor_channel, alpha=self.right_motor_alpha)
                
            def set_motors(self, left_speed, right_speed):
                self.left_motor.value = left_speed
                self.right_motor.value = right_speed
                
            def forward(self, speed=1.0, duration=None):
                self.left_motor.value = speed
                self.right_motor.value = speed

            def backward(self, speed=1.0):
                self.left_motor.value = -speed
                self.right_motor.value = -speed

            def left(self, speed=1.0):
                self.left_motor.value = -speed
                self.right_motor.value = speed

            def right(self, speed=1.0):
                self.left_motor.value = speed
                self.right_motor.value = -speed

            def stop(self):
                self.left_motor.value = 0
                self.right_motor.value = 0

    # SparkFun Hardware
    elif 93 in addresses:
                
            def __init__(self, *args, **kwargs):
                super(Robot, self).__init__(*args, **kwargs)
                
                self.motor_driver = qwiic.QwiicScmd()
                self.left_motor = Motor(self.motor_driver, channel=self.left_motor_channel, alpha=self.left_motor_alpha)
                self.right_motor = Motor(self.motor_driver, channel=self.right_motor_channel, alpha=self.right_motor_alpha)
                self.motor_driver.enable()
                
            def set_motors(self, left_speed, right_speed):
                self.left_motor.value = left_speed
                self.right_motor.value = right_speed
                self.motor_driver.enable()
        
            # Set Motor Controls: .set_drive( motor number, direction, speed)
            # Motor Number: A = 0, B = 1
            # Direction: FWD = 0, BACK = 1
            # Speed: (-255) - 255 (neg. values reverse direction of motor)
            
            def forward(self, speed=1.0, duration=None):
                speed = int(speed*255)
                self.motor_driver.set_drive(0, 0, speed)
                self.motor_driver.set_drive(1, 0, speed)
                self.motor_driver.enable()

            def backward(self, speed=1.0):
                speed = int(speed*255)
                self.motor_driver.set_drive(0, 1, speed)
                self.motor_driver.set_drive(1, 1, speed)
                self.motor_driver.enable()

            def left(self, speed=1.0):
                speed = int(speed*255)
                self.motor_driver.set_drive(0, 1, speed)
                self.motor_driver.set_drive(1, 0, speed)
                self.motor_driver.enable()

            def right(self, speed=1.0):
                speed = int(speed*255)
                self.motor_driver.set_drive(0, 0, speed)
                self.motor_driver.set_drive(1, 1, speed)
                self.motor_driver.enable()

            def stop(self):
                self.motor_driver.set_drive(0, 0, 0)
                self.motor_driver.set_drive(1, 1, 0)
                self.motor_driver.disable()

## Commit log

2019-03-18 Update STL files to release ver
    [camera_mount.stl, caster_base.stl, caster_shroud.stl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]
2019-03-30 Rename for 60mm wheel
    Rename existing caster parts designed for 60mm wheels
    [caster_base_60mm.stl, caster_shroud_60mm.stl]
2019-03-30 Update "60mm" caster parts
    [caster_base_60mm.stl, caster_shroud_60mm.stl]
2019-03-30 Add "65mm" caster parts
    Add caster related STL parts designed for 65mm wheels
    [caster_base_65mm.stl, caster_shroud_65mm.stl]
2019-03-30 Add STEP and IGES files to "open-source"
    Add STEP and IGES files to "open-source" the hardware design
    [JetBot-0314_60mm.step, JetBot-0314_65mm.step]
2019-04-02 Rename IGES and STEP files
    Rename IGES and STEP files as suggested in PR review
    [jetbot_60mm.step, jetbot_65mm.step]
2019-06-03 fixed xy/steering typo
2019-08-22 Add STEP and IGES files for camera mount
    [camera_mount.iges, camera_mount.step]
2020-08-14 Capture CSI camera at lower res to reduce RAM footprint
2020-08-20 Pin traitlets to a version (Jun 15, 2020)
2020-08-20 Fix the data collection cell by reviving couple of lines
2020-08-26 removed opencv camera, use GST python api instead
2020-08-26 added hardware accelerated jpeg encoder
2020-08-26 added zmq camera publisher/subscriber
2020-08-26 clean shutdown on keyboard interrupt
2020-08-26 copy=true and sensor-mode=0
2020-08-27 added zmq camera, with opencv as default
2020-08-27 added camera widget convenience helper
2020-08-27 added conflate option to allow dropping of old frames
2020-08-29 made zmq camera default
2020-08-31 Add setup script to configure Jetson as docker host for JetBot
2020-09-01 Rename the jetson configure script
2020-09-04 revert default camera
2020-09-04 default camera gst and handle Camera args
2020-09-26 Change color scheme and navigation structure
    [camera_mount.iges, camera_mount.step, camera_mount.stl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]
2020-09-26 Add camera.stop() in notebooks that use camera
2020-09-26 Add another IMX219 camera option
    [camera_mount.iges, camera_mount.step, camera_mount.stl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]
2020-09-28 Add a flow chart in Getting Started page
2020-09-29 Switch link to wiki to the new doc site
2020-10-22 Retain the maximum FoV of camera while keeping the minimum RAM consumption
2020-10-22 Update bill_of_materials.md
    updated wording in BOM wifi notices
2020-11-09 Handle the new revision of Waveshare board
2020-12-29 Added some comments to highlight Waveshare specific code
    Motor.py includes specific code to control the Waveshare JetBot board (as it differs from the AdaFruit motor controller with reference to pin numbers). Added comments to make this clearer.
2021-01-05 Use camera.width and camera.height instaed of a fixed number
2021-01-05 added landing page GIFS directly to repository
2021-01-08 Pin JupyterLab to 2.2.6
2021-01-15 Missing 'os' import
    The os import was missing, leading to an exception, so the selected camera was always opencv_gst_camera.
    Replaced the try/catch by a get with default.
2021-02-16 Insert a note on JetPack 4.5 bootloader update
2022-02-03 Add SparkFun hardware support (#467)
    * Add SparkFun hardware support
    Adds support for hardware included in SparkFun kit
    * Fix no return issue
    Sets variables to None in the event that get_ip_address() fails
    * Revert "Fix no return issue"
    This reverts commit 170ea59a4ca81c88823eadcffb1af0d31b847e5d. Issue resolved in this commit: https://github.com/NVIDIA-AI-IOT/jetbot/commit/436755b244f3a8736b5b73417322f99b0a420bd9
    [motor.py, robot.py]
2024-04-30 Add Orin Nano version of BoM page
2024-05-07 Add notes on original Jetson Nano EOL
2024-10-04 Add a message to explain images are currently not available
